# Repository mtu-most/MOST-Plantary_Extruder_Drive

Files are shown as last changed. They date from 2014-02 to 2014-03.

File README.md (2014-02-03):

<h1>MOST Planetary Extruder Drive</h1>
<p>This is derived from Airtripper's Bowden extruder drive (http://airtripper.com/1071/airtrippers-bowden-extruder-v3-updated-design/).
</p>
<p>
It resolves:
* Torque issues - print speed can limited by torque of the drive motor. The 4.62:1 planetary gearbox overcomes this.
* Inability to live-feed new filament - the original design had the filament path too far into the drive gear pretty much eliminating the possibility of live-feeding filament through the drive. The filament path has been moved and an infeed sheath was added to facilitate live feeding.
</p>

<h2>Bill of Materials</h2>

<p>Printed parts:</p>
<ul>
<li>Sun gear (1)</li>
<li>Planet gear (3)</li>
<li>Planetary carrier (1)</li>
<li>Input half (1)</li>
<li>Output half (1)</li>
<li>Motor end (1)</li>
<li>Extruder end (1)</li>
<li>Idler shaft (1)</li>
<li>Idler housing (1)</li>
<li>Linking bar (1)</li>
</ul>
<p>Hardware:</p>
<ul>
<li>624z bearing (3)</li>
<li>625 bearing (1)</li>
<li>608zz bearing (1)</li>
<li>MR105z bearing (1)</p>
<li>M4 x 16mm socket head cap screws (3)</li>
<li>M4 nylock nuts (3)</li>
<li>M4 flat washers (9)</li
<li>M3 x 8mm set screw (1)</li>
<li>M3 nut (8)</li>
<li>M3 x 40mm socket head cap screw (3)</li>
<li>M3 flat washer (9)</li>
<li>M3 x 12mm socket head cap screw (4)</li>
<li>M3 x 20mm socket head cap screw (2)</li>
<li>M3 x 45mm socket head cap screw (2)</li>
<li>1/4" fuel hose (25mm)</li>
<li>M5 x 40mm hex head cap screw (1)</li>
<li>Mk7 drive gear (1)</li>
<li>NEMA17 stepper motor (1)</li>
</ul>

<h2>Printing</h2>
Print gears singly with the planet gears printed on a raft to maintain shape of teeth on first layer. Print slowly with lots of cooling.

<h2>Assembly</h2>
<p>All of the case parts are printed with an arrow-shaped screw boss to indicate how the pieces are aligned when assembled.</p>
<p>Assemble planetary carrier first. Press 624z bearings into planetary gears. Put M4 screws through the bearing and then place three washers on each screw. Push the M5 screw into the planetary carrier fully seating the head of the screw in the recess provided. Press M4 nylock nuts into the planetary carrier and thread the screws into the nuts. Leave the screws very loose so that the planet gears can be moved out of the way to facilitate insertion of sun gear</p>
<p>Press an M3 nut into the nut trap on the sun gear and thread the set screw into the nut. Work the sun gear into the planet gears and then tighten the M4 screws.</p>
<p>Attach the motor end to the NEMA17 motor with the M3 x 12mm screws, each with a washer.</p>
<p>Press the sun gear side of the planetary carrier assembly into the input half. Press the output half onto the opposite side of the planetary carrier assembly. Place the 625 bearing in the pocket on the extruder end. Press a pair of M3 nuts into the recesses on the inlet side of the extruder end where the linking bar will go. Attach the linking bar with the M3 x 30mm screws. Pass the M5 screw extending from the plantary carrier through the 625 bearing. Rotate the gear box several times to clean the teeth and ensure that everything moves properly.</p>
<p>Align the flat side of the shaft relief in the sun gear (where the set screw is) with the side of the motor end having the set screw access hole in it (opposite the arrow-shaped screw boss). Align the motor shaft and press the sun gear onto it compressing the entire case assembly until there is little gap between them. Pass the M3 x 40mm screws with washers on them through the holes in the cases and affix M3 nuts to them. Do not tighten the nuts too much. Tighten the set screw in the sun gear against the motor shaft. Spray white lithium grease into the case and rotate the gearbox such that all of the gears are coated with lubricant.</p>
<p>Put the Mk7 drive gear on the M5 screw. Pass filament through the path and ensure that the gear is properly aligned. Tighten the set screw in the drive gear. Drill a pair of 3mm holes in the fuel line aligning them with the slots in the idler housing. Attach the fuel hose to the extruder end with a pair of M3 x 45mm screws with washers in the hose side. Attach the idler to the extruder end, tucking the M3 x 45mm screws into the slots on the idler housing.</p>
<p>Exercise the drive with no filament in it or several minutes to ensure that motion is smooth and no binding occurs. Tighten the case screws and check again for binding. If the gear box binds, loosen the case screws.</p>

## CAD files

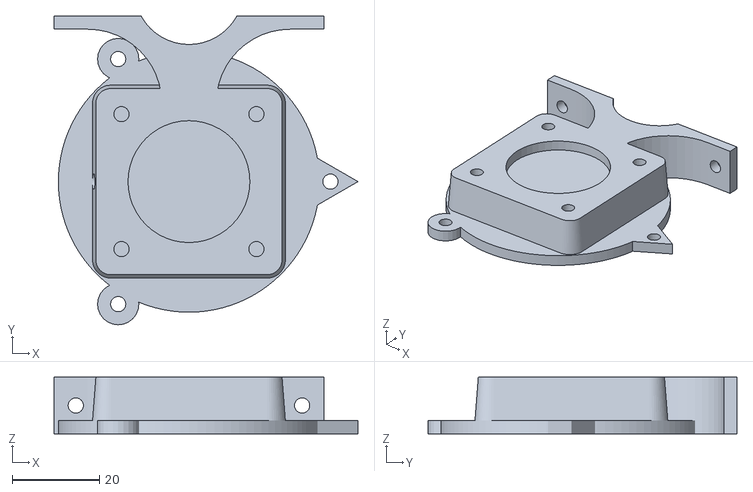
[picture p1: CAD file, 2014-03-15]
end_motor_v_mount.stl
69.8 x 70.9 x 13.0

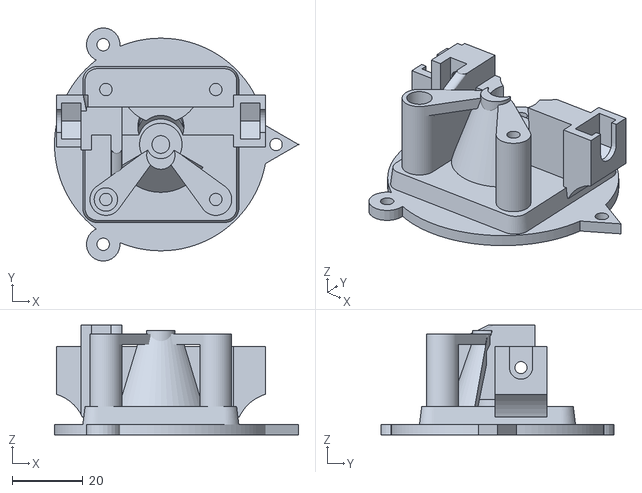
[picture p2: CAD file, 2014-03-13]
planetary_mount_3mm.stl
68.8 x 65.8 x 31.0

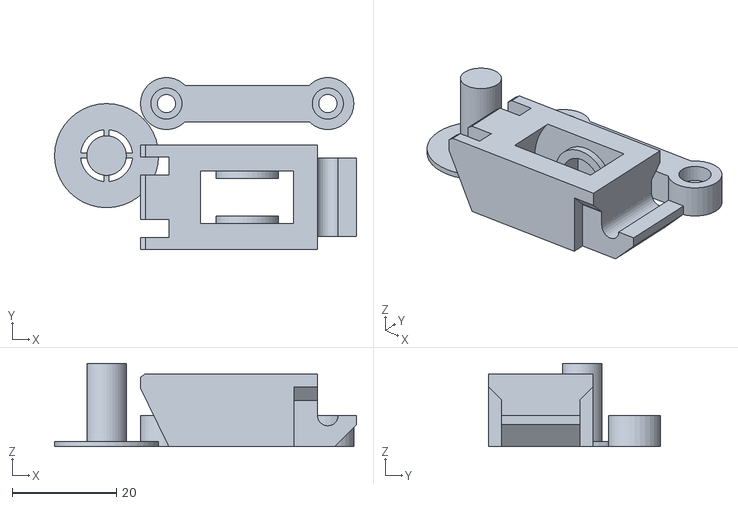
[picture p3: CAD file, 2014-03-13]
axle_idler_link.stl
58.0 x 33.0 x 16.0

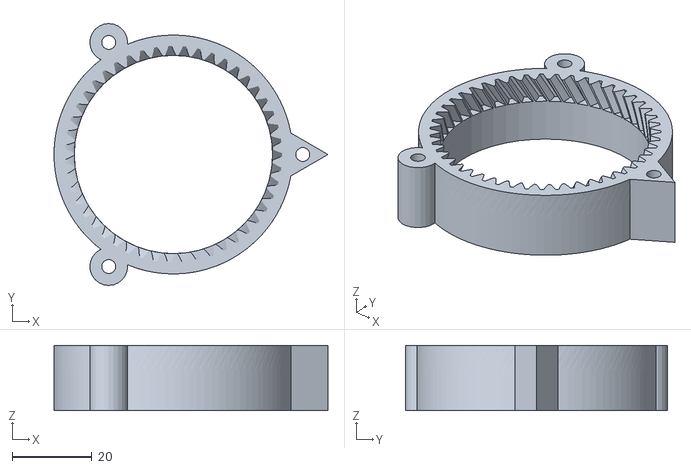
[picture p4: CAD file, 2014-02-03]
output_half.stl
68.8 x 65.8 x 16.4

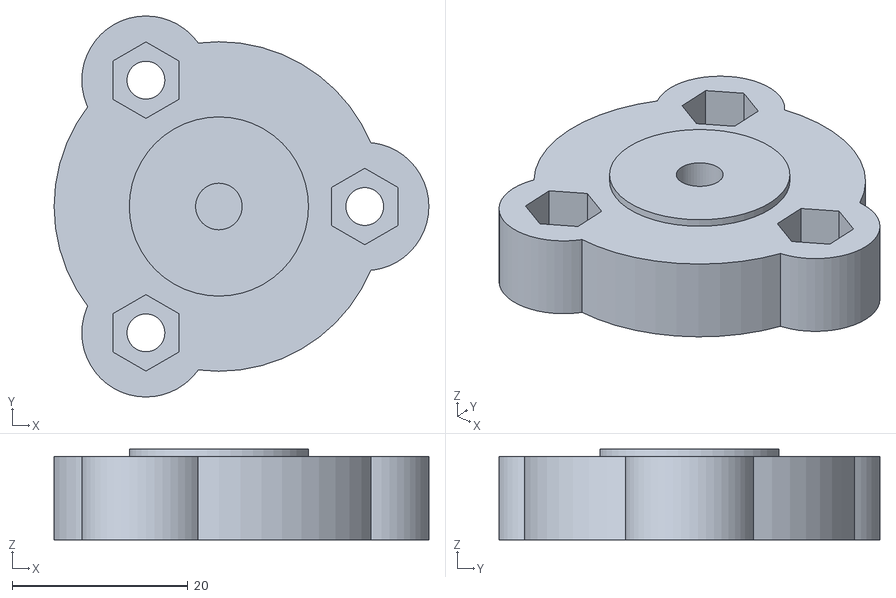
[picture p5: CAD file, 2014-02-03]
planetary_carrier.stl
42.6 x 43.3 x 10.3

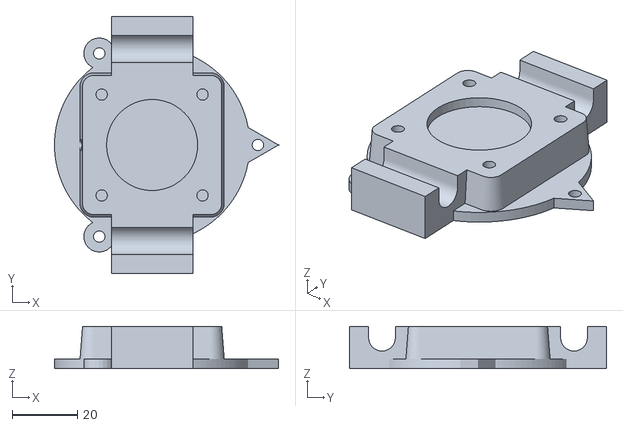
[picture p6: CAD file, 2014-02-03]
end_motor_h_mount.stl
68.8 x 79.0 x 13.0

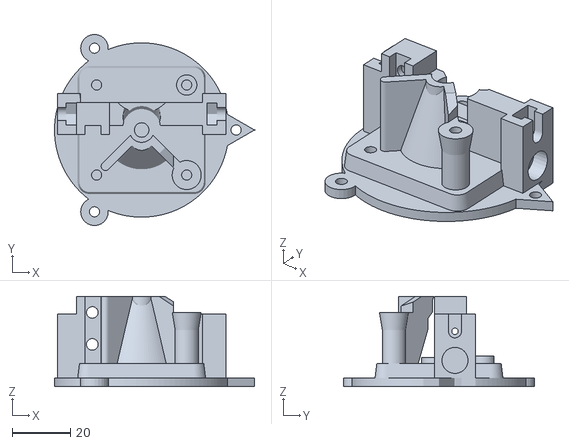
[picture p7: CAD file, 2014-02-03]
extruder_end.stl
68.8 x 65.8 x 31.0

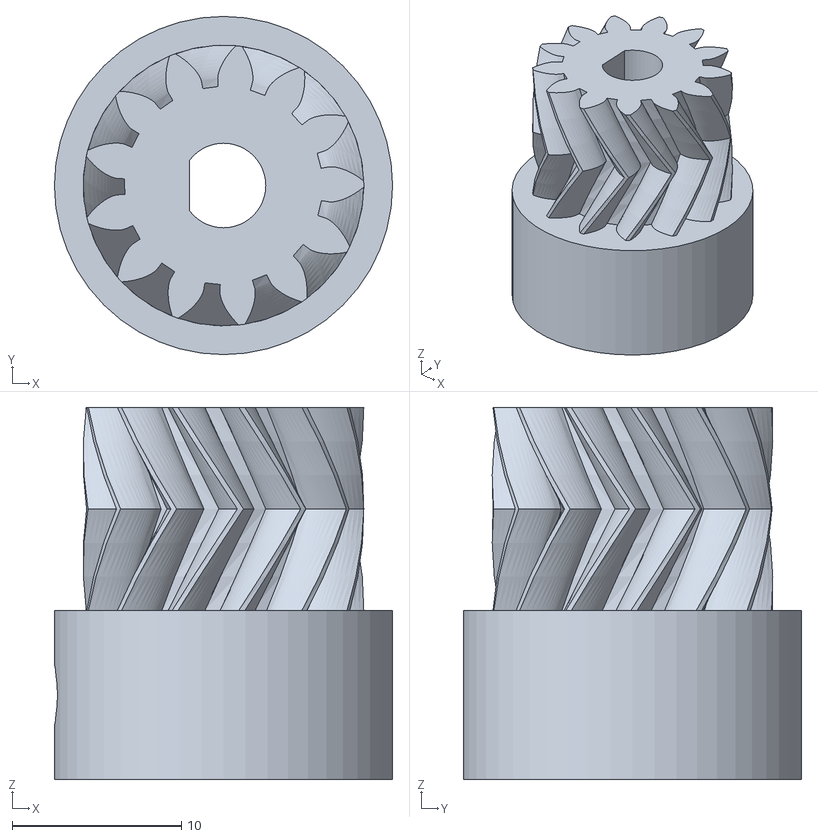
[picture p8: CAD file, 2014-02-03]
sun.stl
20.0 x 20.0 x 22.0

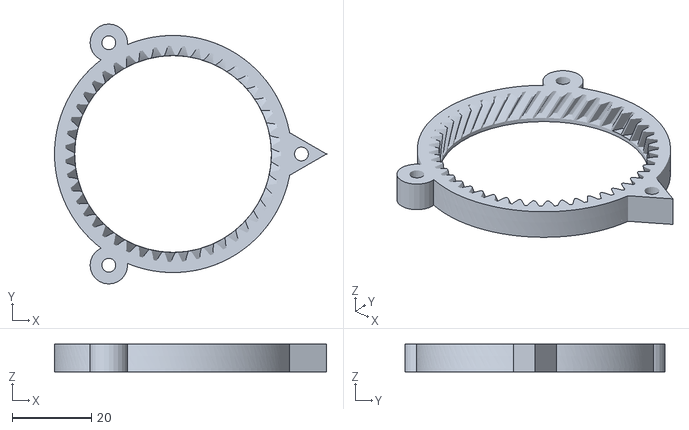
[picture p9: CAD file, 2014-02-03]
input_half.stl
68.8 x 65.8 x 7.00

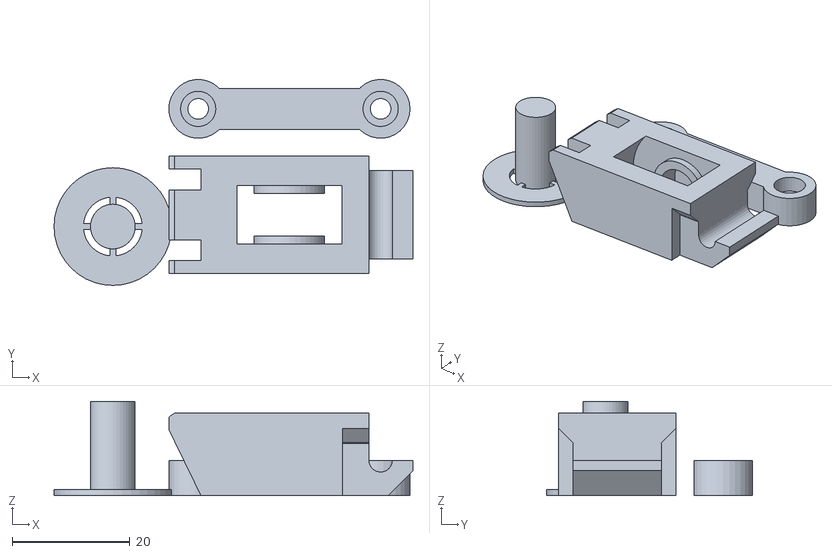
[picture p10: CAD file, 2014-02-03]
idler_shaft_housing_link.stl
61.0 x 35.0 x 16.0

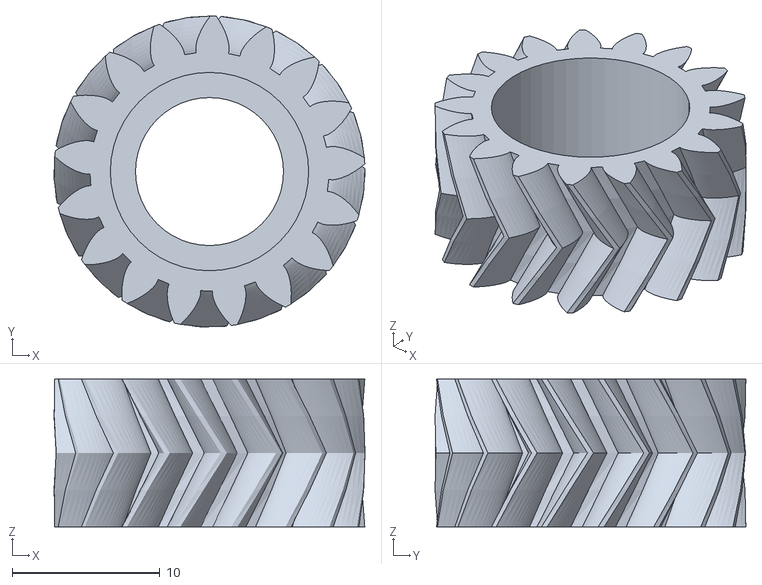
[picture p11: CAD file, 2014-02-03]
planet.stl
21.0 x 21.0 x 10.0

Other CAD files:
planetary_mount_1.75mm.stl

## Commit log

2014-03-13 updated extruder end
    [axle_idler_link.stl, planetary_mount_1.75mm.stl, planetary_mount_3mm.stl]
2014-03-15 updated motor ends
    [end_motor_h_mount.stl, end_motor_v_mount.stl]
